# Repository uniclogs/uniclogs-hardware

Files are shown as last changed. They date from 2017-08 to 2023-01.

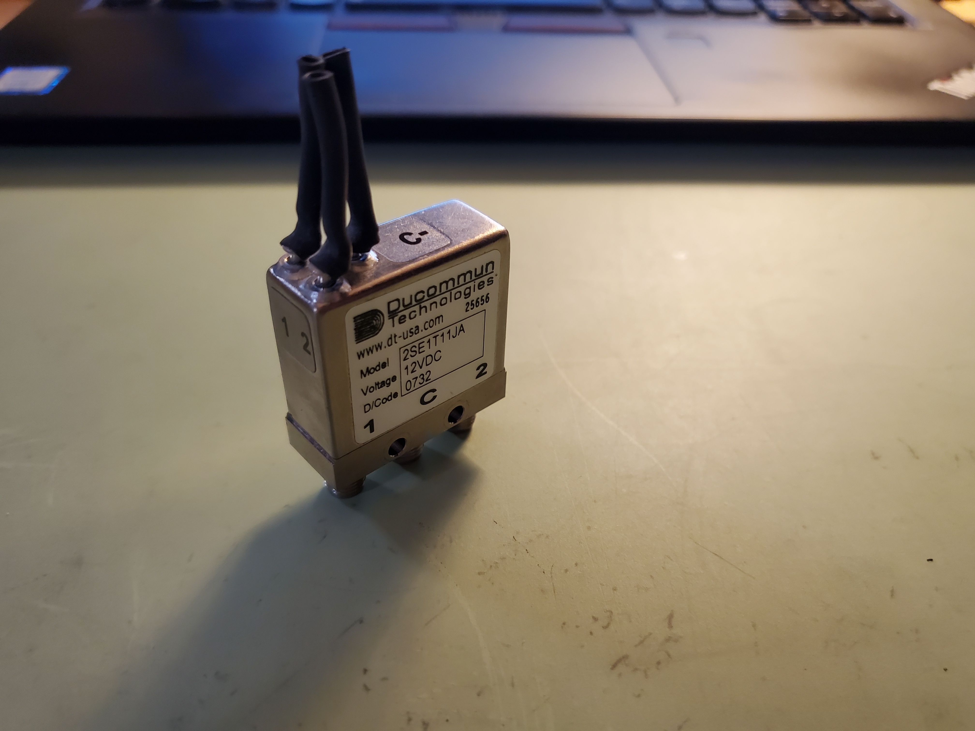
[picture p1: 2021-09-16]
eb-ground-station/rf-systems/components/rf-relay/20210714_223024.jpg

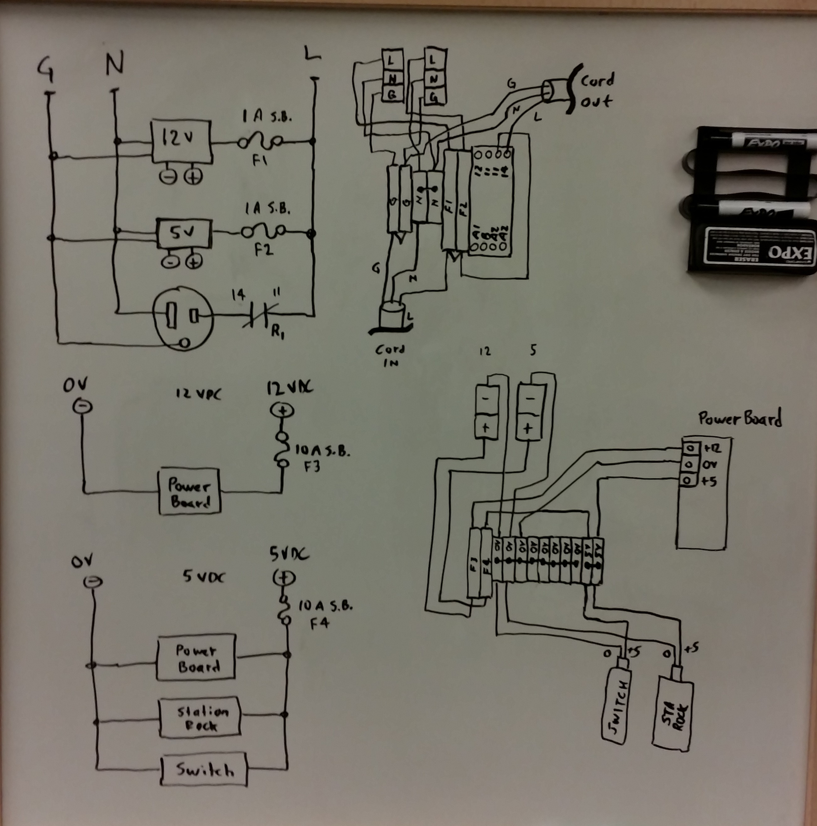
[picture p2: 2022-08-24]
eb-ground-station/power-system/power_wiring_diagram_1a.jpg

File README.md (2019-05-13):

# University Class Open Ground Station
UniClOGS ground station hardware for both RF and antenna positioning

EB Station Block Diagram

EB Station Block Diagram

## OreSat Ground Station Infrastructure

OreSat will utilize two ground stations for this project, a primary station, and a fully-capable secondary station. The primary station is being constructed by the students involved in the project and will be located on the Portland State University Engineering Building. The secondary station is an existing amateur satellite ground station located at a different location for spatial diversity. It can be used to help verify and check out the primary station as construction progresses, and serve as a backup to the primary station. The two stations are identical.

## RF Links

The ground station infrastructure provides two communications functions between the ground and the spacecraft, (1) downlink communications on UHF for the Telemetry Beacons and Command Responses from the spacecraft, (2) uplink communications on L-Band for the Commands to the spacecraft, and (3) downlink communications on S-band for mission payload and camera data.

The UHF component is centered in the 435 to 438 MHz amateur spacecraft service band and utilizes a circular polarized directional Yagi antenna with a RHCP/LHCP polarization sense switch. The L-Band component is centered in the 1260 to 1270 MHz amateur spacecraft service band designated for uplink only, and utilizes a RHCP circular polarized 2x2 helix array. All of this is mounted on an azimuth/elevation antenna positioner. A coax switch connects the UHF antenna to either a Low Noise Amplifier (LNA) for receiving, or a Power Amplifier (PA) for transmitting. The LNA and PA is then connected to a Software Defined Radio (SDR) that provides both UHF RF input and output signals. The L-Band antenna is directly connected to a PA for transmitting only, and then to the same SDR to provide the L Band RF signal.

The S-Band component is centered on 2.4 to 2.43 GHz amateur spacecraft service spectrum. A 0.5 meter parabolic reflector with a RHCP/LHCP feed is mounted on the same antenna positioner as the UHF and L-Band antenna. A coax switch is used to select RHCP or LHCP signal from the feed, is then fed to a bidirectional PA/LNA. The PA/LNA is connected to a ATH9K IEEE 802.11b adapter that provides both the S-Band RF downlink receiver and uplink transmitter signals.

The SDR used for UHF and L-Band is the LimeSDR from LimeMicro, which utilizes GnuRadio for modulation and demodulation. The emission type is GFSK at 50 kb/s, and was chosen for the capability of the Engineering transceiver radio on the spacecraft, an acceptable performance indicated by the link budget, and is somewhat common in the amateur satellite community.

## Antenna positioner

An antenna positioner controller is used to aim the antenna array and is interfaced serially using the EasyComm control protocol accessible through the HamLib control library. The positioner controller is based on the Open Source hardware/software project by K3NG, and provides the ability for tracking control through HamLib _rotctld_ both locally using GPredict, or by the SatNOGS Client software which provides interconnectivity to the SatNOGS system over the Internet.

## GnuRadio 

Data is passed into/out of the ground station radio through GnuRadio ModCod blocks and can provide raw IQ sample files from the payload data. Doppler shift can be compensated for in real time using the tracking software and an XML/RPC server in GnuRadio.

## Data

The Engineering Control/Telemetry subsystem provides telemetry data to the ground in two forms, a GFSK modulated data frame in response to a command request, and a very short Morse code (CW) modulated telemetry sequence and satellite ID if no activity is present for a given period of time. This Morse code ID allows the satellite to be heard by the general amateur radio community and will help with identifying the satellite once on orbit. There are several satellite housekeeping commands that can be sent up from the ground to control power, attitude and payload functions, and most importantly a command to reliably shut off all RF transmissions if required. All commands up to the satellite are authenticated for security.

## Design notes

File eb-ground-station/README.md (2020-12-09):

## EB ground station subsystems

Subsystems pertaining to the Engineering Building "University Class" Open Ground Station (UniClOGS)

Major components

* Structure
* Antennas
* RF systems
* Network
* Power system
* Tracker
* Lightning protection

## BOM for ground station

<!-- [Here is the Bill of Materials so far](https://docs.google.com/spreadsheets/d/1EBKyHZEIYpfHariDGcVJl7H6Yc5BHaDegu6B_IkEdFo/edit#gid=687688620) --->
[Here is the Bill of Materials](https://docs.google.com/spreadsheets/d/1g-H72wh_L9K5FMgDF-K87dqiwulbmqTZjYWP18Jh5gg/edit#gid=1275452567)

The BOM is divided into six sections organizing to some degree what's needed in each phase of the construction.

| Code | Phase of construction |
| --- | --- |
| SDR | Test SDR and GR |
| PANEL | Build station panel |
| POS | Build K3NG positioner controller |
| ANT | Antenna components and feedline |
| ROOF  | Roof structures and appurtenances |
| OPER  | Operations equipment |

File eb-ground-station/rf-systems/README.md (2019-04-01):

## RF Components

* Antennas
* Feedlines
* Low Noise Amplifier
* Power Amplifier
* Software Defined Radio (SDR)

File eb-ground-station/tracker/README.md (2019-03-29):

## Tracker used with UniClOGS

### This is based on the K3NG Rotator Controller

The ground station uses an Arduino and simple interface shield to convert the serial
"Easycom protocol" that _rotctld_ speaks, into the relay output and potentiometer
input expected by the Yaesu G5500 rotator control box.

K3NG has provided an open source solution implementing this Arduino code.

This repo contains some simple instructions on how to get the code, a description of the shield,
and the settings needed by the UniClOGS hardware.

See:  https://github.com/k3ng/k3ng_rotator_controller

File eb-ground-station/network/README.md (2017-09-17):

## Establish OreSat VLAN (aka "Blue Pipe")

- Essentially the "Blue Pipe" is a 1 Gb/s VLAN between the EB Penthouse rack and EB. This is officially called the OreSat VLAN.

- Also related is the edge router and firewall to get us out to the Internet.

### Provide a "what we want" document to Dave Burns to move forward with getting the connection established.

- Dave expects to need a pair of Single Mode SFP's to increase the existing bandwidth over the fiber between the Penthouse switch and the EB switch on LL. He's planning on moving from the MultiMode fiber to SingleMode fiber, since MM over the fiber they have installed won't support Gb over the required distance. They have both MM and SM available at both FTB's. Estimated $250 each.

- Estimate the bandwidth we need given the devices on the roof only push I/Q samples from the SDR to the server in EB-91, and doing all the signal processing on the server. Expected this will go across UDP.

- Describe the protocols and ports we want to move across the VLAN, and what we want to push across the edge router.

   * We expect only ports 22, 123 (NTP) and 443 across the edge router.
   * Essentially answer his question "What are you wanting to put on 'my' network?"
      * Since this is a VLAN, our traffic would never really appear on his network, however what goes out through the firewall and onto the Internet is what he is really asking about.

NB: Dave expressed keen interest in getting NTP from our time server. Maybe also provide PTP?

[Miles started this document](https://docs.google.com/document/d/1XI038USdZ7fAQvtVEo2skS9kDt9Eve8YVRDrkvMqaz0/edit)

### Follow through in getting the LAN physically connected and working.

- There needs to be a 1 Gb/s switch in the rooftop enclosure to provide LAN to both of the GS devices in our enclosure. The weather station will use it's own physical CAT-6 circuit to the Penthouse Cisco switch, so it does not enter onto any of our concerns. 

- There currently is a connection in the EB penthouse using CAT-6 to the rooftop.

- There will need to be a connection in a comm closet adjacent to EB-91 to some structured wiring connection and wall plate on EB-91. It will need to be labeled **_OreSat VLAN_**.

### Establish the OreSat server assets in EB-91

- We should expect to put all of our devices in a small 19 inch rack somewhere in the EB-91 lab

- We will want another 1 Gb/s switch in that rack for all things that need to connect to OreSat VLAN

- There will also need to be a connection back to "Dave's Network" where we connect our edge router between the two. Here another structured wiring jack on EB-91 will be needed, and should be labeled **_Dave's Network_** or something like that.

- I would recommend a Juniper SRX-100 for use as the edge router / firewall for the following reasons.
   * We only need 100 Mb/s out to the Internet.
   * It could setup several security zones
   * Low cost, and highly capable packet filtering

Originally identified this issue on: 20-May-2017

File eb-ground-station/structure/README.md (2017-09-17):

## Requirements for Engineering Building Ground Station Structure
### G.N. LeBrasseur  15-Aug-2017

### Introduction

The Portland State University Aerospace Society and Oregon Small Satellite Project (OreSat) propose
to [augment an existing weather station](weather-station-augmented-design/README.md) on the campus Engineering Building. The weather station is an
existing structure having been in place for several (maybe 4) years, and is in reasonably good physical
condition. It was suggested that this structure could be utilized to provide the physical support for the
proposed satellite ground station antenna on a co-site basis in order to fit within the economic constraints
on the OreSat project.

The design drawing *GS_Structure_1_1* illustrates the existing mast structure, and the proposed changes of
augmenting for the proposed co-site use. Page 3 of 3 of this document indicate the changes in red.

### Expected Loads

The appurtenances or components of the existing weather station have not been described in the drawing, primarily
because it is expected they pose minimal wind or structural load. It is expected that the predominant wind load would be presented
by the ground station antenna array which would be mounted at the top of the augmented structure on page 3 of 3.

The intent of the design is to sustainably survive a continuous wind load of 100 mph or less without damage or failure.

The physical wind load is expected to be within the following:

#### From manufacturer data sheet

 * 70 cm antenna [1] : 2.0 ft^2 at 100 mph
 * 2 meter antenna [2] : 2.5 ft^2 at 100 mph

#### Extended analysis

Upon conversation with the manufacturer it was discovered they did not have a specification of their product for
wind loads with ice. Being in the Pacific Northwest where ice is expected as normal, particularly when wind speeds
might be at their highest, a wind load with ice margin is applied as two (2) times the non-ice wind load value.

So for a wind load with ice safety margin, the following values should be used;

* 70 cm antenna: 2.0 ft^2 at 100 mph * 2 = 4.0 ft^2 at 100 mph
* 2 m antenna:  2.5 ft^2 at 100 mph * 2 = 5.0 ft^2 at 100 mph

**Total wind load: 4.0 + 5.0 = 9.0 ft^2 at 100 mph**

It is thereby anticipated that applying this wind load at the very top hight of the mast as described on page 3 of 3
would describe the extreme structural requirements of this system.

### References

* [70 cm] antenna  
* [2 m] antenna
* 22 foot [cross boom]

[70 cm]: http://www.m2inc.com/amateur/436cp42ug-420-440-mhz/
[2 m]: http://www.m2inc.com/amateur/2mcp22-144-148-mhz/
[cross boom]: http://www.m2inc.com/crossboom-hd-fg-11/

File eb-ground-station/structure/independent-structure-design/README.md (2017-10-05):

# Structural Stuff for the Stand-alone EB Ground Station

As per a conversation between Glenn and Joe on 2017-9-22, we're switching to a slightly smaller set of antennas. 
This lets us drop about 3 ft^2 from the frontal area of each antenna and a few feet of height, while only loosing 3 dB.
There's a [BoM in the tomes of the dark lord Goagh'le.][BoM]

Included are drawings of the roof layout, and the datasheet for the Rohn non-penetrating antenna mount.

[BoM]: https://docs.google.com/spreadsheets/d/1EBKyHZEIYpfHariDGcVJl7H6Yc5BHaDegu6B_IkEdFo/edit#gid=687688620

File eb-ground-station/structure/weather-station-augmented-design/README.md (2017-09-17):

## Utilize existing mast

We want to determine what we need to do to rebuild the station structure in order to co-site both the OreSat ground station, and the weather station maintained by Prof. Elliott Gall.

There is a drawing in this repo that shows both the existing mast structure, and the augmented structure. We should have someone with structural expertise look over this drawing set. The intent is to extend the mast using a 15 foot section of 1-1/4 inch SCH 80 6061 aluminum pipe, and add a set of additional struts. The augmented parts are in red on page 3 of 3 of the set.

## Utilize existing utilities.

* There is a weather rated 120 volt 20 amp duplex GFI receptacle available, and one outlet is used for the weather station. The second outlet could be utilized for our service.

* There are two CAT-6 / RJ-45 receptacles available in a weather rated box, one of which is used by the weather station. The second one could be utilized for our needs. These CAT-6 circuits make their way through structured wiring to the penthouse communications rack, whereby they terminate at a patch panel next to a network switch.

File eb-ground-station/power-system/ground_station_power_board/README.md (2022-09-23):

# Station Power Board

This board controls all of the switching of power to components in the ground station.
It accepts it's commands through an I2C interface on the Stationd computer.

The switching is acomplished through 3 I2C GPIO device setup as 24 output bits. The
bits control mosfet switches provideing both 5VDC and 12VDC circuits.

The board also has an A/D to monitor the RF Power Amplifiers output power detectors. The
characteristics of this power measurement is detailed in the power amplifier testing
spreadsheet unfer RF-systems.

Finally this board provides a temperature measurement of the system enclosures environment.

See further documentation in the docs folder

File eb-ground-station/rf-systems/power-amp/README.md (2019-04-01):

### Linear power amplifier

Power amplifiers using hybrid power amplifier modules from
Mitsubishi or Hitachi are used to drive the antenna.

See:
* 2m:   Hitachi SAV33 MOSFET
* 70cm: Hitachi SAU83L MOSFET
* 23cm: Mitsubishi RA18H1213G
   https://www.mitsubishielectric-mesh.com/products/pdf/ra18h1213g.pdf

Testing data is included in the spreadsheet, including characteristics of the power output monitor voltage.

* 2 meter
   https://www.downeastmicrowave.com/product-p/2m30pack.htm

* 70 cm
   https://www.downeastmicrowave.com/product-p/7025pack.htm

* 23 cm
   https://www.downeastmicrowave.com/product-p/2330pack.htm

Additionally, the output of the LimeSDR is a little too low to fully drive the power amplifires, so inline MMIC
amplifiers are placed in between.

* 2m: MiniCircuits GALI-49 (packed in their development test board TB-409-49+)
   https://www.minicircuits.com/WebStore/dashboard.html?model=GALI-49%2B
   https://www.minicircuits.com/pcb/WTB-409-49+_P02.pdf
    
* 70cm: MiniCircuits GALI-49 (a second one)

* 23cm:  MiniCircuits ZRL-1150LN
   https://www.minicircuits.com/WebStore/dashboard.html?model=ZRL-1150LN%2B

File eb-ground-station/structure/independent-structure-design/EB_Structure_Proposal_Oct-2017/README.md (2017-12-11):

## Proposal for Engineering Building Ground Station
### October 2017

* Narrative of proposal
* General location of site on Engineering Building
* Detailed drawings of site
* Data sheet for non-penetrating mast
* Quote for mast

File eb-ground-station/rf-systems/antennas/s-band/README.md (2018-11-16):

## S Band antenna

* Parabola
* Radome
* 90 degree hybrid
* Testing results

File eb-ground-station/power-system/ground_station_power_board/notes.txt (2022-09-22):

New Design Requirements:
* Use MAX7310ATE 8 bit GPIO expander
* 24 control bits, exact setup TBD
* Switches:
  - Low side
  - High side
  - High side, high current
  - High side, high current, soft start
* Designed in KiCad
* Use the correct I2C RasPi pins
* Connectors; all seperable, push-lock lever or spring type:
  - Power in: 3pos 1row 12AWG
  - GPIO x3 : 8pos 1row 12-26AWG
  - ADC     : 4pos 2row 22AWG
* All 4 UARTs on the pi need to be broken out to their own ports to be passed on to other stuff
* Current ranges should be configurable in hardware after the PCB has been fabbed

Some notes on the new design:
Up to 2 of these boards can be put in paralell simply by connecting the 40pin connectors in paralell and jumping different address jumpers on each board.

Parts: (may be out of date list to what was actually ordered)
+---------------------------------+------------------+-----------------+
| Name                            | MFR              | MPN             |
+---------------------------------+------------------+-----------------+
| 8 pos wire  connector large     | Phoenix Connect  | 1942549         |
| 8 pos wire  connector small     | Phoenix Connect  | 1851290 1966156 |
| 8 pos board connector large     | Phoenix Connect  | 1924143         |
| 8 pos board connector 45° small | Phoenix Connect  | 1827486         |
| 8 pos board connector small     | Phoenix Connect  | 1827923         |
| GPIO expander                   | Maxim Integrated | MAX7310ATE      |
| I2C ADC                         | TI               | ADS1115         |
| I2C temperature sensor          | Microchip        | MCP9808         |
| Dual N-Channel MOSFET           | Diodes Inc       | DMN61D8L-LVT    |
| P-Channel MOSFET                | Vishay Siliconix | SUD50P08-25L-E3 |
| Dual 1.5A MOSFET Driver         | Microchip        | TC427           |
+---------------------------------+------------------+-----------------+

Connectors (Phoenix Connect):
+---------------------------------+---------+------+----+--------+-----+-------------+
| Name                            | Number  | Pins | A  | Pitch  | Ang | Connector   |
+---------------------------------+---------+------+----+--------+-----+-------------+
| 3 pos wire  connector huge      | 1996139 | 3    | 41 | 7.62mm | 0°  | PC 5        |
| 8 pos wire  connector large     | 1942549 | 8    | 16 | 5.08mm | 0°  | MSTB 2,5 HC |
| 8 pos wire  connector small     | 1748419 | 8    | 8  | 3.81mm | 0°  | MC 1,5      |
+---------------------------------+---------+------+----+--------+-----+-------------+
| 3 pos board connector huge      | 1720806 | 3    | 41 | 7.62mm | 0°  | PC 5        |
| 8 pos board connector large     | 1924143 | 8    | 16 | 5.08mm | 0°  | MSTB 2,5 HC |
| 8 pos board connector small     | 1827923 | 8    | 8  | 3.81mm | 0°  | MC 1,5      |
| 8 pos board connector 45° small | 1827486 | 8    | 8  | 3.81mm | 45° | MC 1,5      |
+---------------------------------+---------+------+----+--------+-----+-------------+

Configuration of the Outputs:

Populate and leave some components unpopulated to configure the output current modes.
Only the dual mosfet or the mosfet driver may be populated, never both for the same channel pair
If the dual mosfets are populated, the rest of the circuit may be configred independently for the two channels 
If you populate the dual mosfet, also populate the 1k resistors on its gate.
If you populate the P channel MOSFETs, populate the 10k pullup resistors

Possible current modes: (+ is current out, - is current in)
±1.5A
-500mA
+15A

The channel pair may be configured for EITHER {±1.5A} or {-500mA or +15A}

To configure for:
+---------+-------------+-------------+----------+-------+-----+-------------+
| Mode    | Dual Driver | Dual MOSFET | P MOSFET | Rgate | C   | 2pad jumper |
+---------+-------------+-------------+----------+-------+-----+-------------+
| -500mA  |             | yes         |          |       |     | jumped      |
| +16A    |             | yes         | yes      | 1k    |     | open        |
| 16Asoft |             | yes         | yes      | 680k  | yes | open        |
| ±1.5A   | yes         |             |          |       |     | any         |
+---------+-------------+-------------+----------+-------+-----+-------------+

Use the 3pad jumper to select 5 or 12v for the +15A mode
In soft start mode, adjust Rgate to adjust soft start time

RasPI pins:
  +------------+----+----+------------+
  | 3v3        | 01 | 02 | 5V         |
  | SDA        | 03 | 04 | 5V         |
  | SCL        | 05 | 06 | GND        |
  | TX3        | 07 | 08 | TX0        |
  | GND        | 09 | 10 | RX0        |
  |            | 11 | 12 |            |
  |            | 13 | 14 | GND        |
  |            | 15 | 16 |            |
  | 3v3        | 17 | 18 |            |
  |            | 19 | 20 | GND        |
  | RX4        | 21 | 22 |            |
  |            | 23 | 24 | TX4        |
  | GND        | 25 | 26 |            |
  | TX2        | 27 | 28 | RX2        |
  | RX3        | 29 | 30 | GND        |
  |            | 31 | 32 | TX5        |
  | RX5        | 33 | 34 | GND        |
  |            | 35 | 36 |            |
  |            | 37 | 38 |            |
  | GND        | 39 | 40 |            |
  +------------+----+----+------------+
* UART1 shares pins with UART0

---------------------------------------------------------------------------------------
Deisgn Review Notes:
(probably not me) Part numbers on block diagram on GH readme
(future stuff) clarify where everything (power/data etc) go

X Maybe start with a block diagram where each one goes to the schematic that is that part]
X no 12v top 5v bottom put next to eachother
X 100u on 3.3v out
X change resistors to squiggly ones
X move pullups to where they are used
X add another ferrite bead to 12v input to the 3.3v regulators (may have to be larger)
X To populate: FB1 is bead. FB2 is link. FB3 is link (by 3.3v regulators)
X Seperate dual MOSFETS - QnA and QnB
X Move IO pulldowns to the power page

Design Review Part 2 Notes:
UniClOGS stands for Uiversity Class Open Ground Station
Glen will go in sometime to check the board size
add nuts to render and check clearance, add keepout zone to to holes, remember to include space for nut driver or spacers on the back
add OreSat logo at the very end since it takes a bunch of time to fill
Add 12,5,3.3,gnd .1in header in lower left corner
Assumme we are purcahsing every possible component for the bill of materials
Check connectors for stock
Move vias outside of small passives when possible
Final silkscreen check
Move all siklscreen to match orentation of part
Change all ferrite beads to 0805 size
Ground loop warning note
Change 3.3v to 500mA

ToDo Wed:
Add 12,5,3.3,gnd .1in header in lower left corner
Assumme we are purcahsing every possible component for the bill of materials
Check connectors for stock
Change all ferrite beads to 0805 size

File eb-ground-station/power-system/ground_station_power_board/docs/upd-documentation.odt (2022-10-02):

UniClOGS Power Delivery Board

Description and Configuration Details - Board rev 2

Benjamin Crall Sep-2022 Doc Rev. 2.0

# Power Outputs:

Output channels can be configured for one of several modes. Output configuration is done by populating or leaving some other components unpopulated. A + denotes a current leaving the board, and a - denotes a current entering the board. Note that all banks do not support all current modes. Do not populate components that are not specified. Ensure that the output current from all outputs on each power input does not exceed the maximum input current.

## Bank A:

### Available modes:

- -500mA
- +16A
- +16A with soft start

### Configuration Instructions:

The channel supports 12-24AWG wire

Each channel may be configured independently

If you populate the P channel MOSFETs, populate the 10k pullup resistors

Use the 3pad jumper to select 5 or 12v for the +16A mode

In soft start mode, adjust Rgate to adjust soft start time

Mode | Dual MOSFET | P MOSFET | Rgate | C | 2pad Jumper
-500mA | Yes | | | | Jumped
+16A | Yes | Yes | 1k | | Open
+16A soft-start | Yes | Yes | 680k | Yes | Open

## Bank B and C:

### Available Modes:

- ±1.5A
- -500mA

### Configuration Instructions:

These channels support 16-26AWG wire

A channel pair is an even channel and the next odd channel (e.g. 0 and 1)

Each channel pair must be configured for the same mode.

Mode | Dual Driver | Dual MOSFET
-500mA | | Yes
±1.5A | Yes

# Power Inputs

## Input:

Power is supplied to the 3 position connector on the left edge of the board. The pinout is

+12V 25A

GND 16A

+5V 16A

The board does not draw or provide any power to the raspberry pi

Each input supports 8-24AWG wire.

## Protection:

Each power input has reverse polarity protection.

There is no overcurrent protection. Be sure to not to draw too much current from single or combination of outputs. See the channel documentation above to see the individual channel output currents.

- Channel A supports up to 18A of total output current on 5V
- Channel A and B share 18A of total output current on 12V
- Channel C has 7A of total output current at 12V independent of channels A and B

## Outputs:

Power indicator LEDs are in the lower left corner of the board. Next to them are power output pins. These pins are capable of 1A each, except for 3.3V which is capable of 250mA

# Analog Inputs

## Main Inputs

Each board has 4 analog inputs available on the top left 8 pin connector. The pinout is

ADC0 | Agnd | ADC1 | Agnd | ADC2 | Agnd | ADC3 | Agnd

Agnd is connected to general ground by the left link at the top of the Analog In section. This link can be replaced by a 0805 ferrite bead if desired.

Be careful to avoid ground loops when connecting to the Agnd pins

## .1” Inputs

The analog inputs are also available on the .1” header above the main connector. The pinout of this connector is

ADC0 | ADC1 | ADC2 | ADC3 | Agnd

# Data Connectors

## 1x IDC 40 pin connector for the Raspberry pi

| 01 | 02
SDA1 | 03 | 04
SCL1 | 05 | 06 | GND
TX3 | 07 | 08 | TX0
GND | 09 | 10 | TX0
TMP_ALERT (GPIO17) | 11 | 12
ADC_RDY (GPIO27) | 13 | 14 | GND
| 15 | 16
| 17 | 18
| 19 | 20 | GND
RX4 | 21 | 22
| 23 | 24 | TX2
GND | 25 | 26
TX2 | 27 | 28 | RX2
RX3 | 29 | 30 | GND
IO_RESET (GPIO6) | 31 | 32 | TX5
RX5 | 33 | 34 | GND
| 35 | 36
| 37 | 38
GND | 39 | 40

The 3.3V and 5V pins on the Raspberry Pi are not connected

## 4 pin I²C1

GND | 3.3V | SCL1 | SDA1

This is the internal I²C bus used to communicate with the card

## 4 pin (2x2) Signals

ADC_RDY | TMP_ALERT
IO_RESET | gnd

## 3 pin Serial

gnd | RX (in) | TX (out)

These headers connect to (from top to bottom) UART0, UART2, UART3, UART4, UART5

UART2 can also double as I²C0. To use this as I²C0, populate R4 and R5, otherwise leave them empty

gnd | SCL0 | SDA0

# Signal Configuration

All I²C devices on the board are connected to I²C1 on the Raspberry Pi.

## Power Output Banks

The power output banks are controlled by MAX7310 I²C expanders. Each power output bank can be configured to 1 of 8 I²C addresses. The I²C address for each bank is between 0x20 and 0x27. The 3 jumpers configure the 3 lower bits of the address, and the binary address is 0100{AD2}{AD1}{AD0}. The default jumpers connect the address pins to SCL (0) and SDA (1). See the datasheet if more addresses are required. Banks A,B and C have the default addresses of 0x20, 0x21, and 0x22. The active low IO_RESET signal is connected to the Raspberry Pi. Ensure that this signal is held high through boot to not reset the expanders. IO_RESET is pulled high by a 4.7k resistor. See the datasheet for device usage.

## ADC

The ADC is an ADS1115IDGS I²C ADC with a default address of 0x48. Use the jumper to select the alternate address of 0x49 if required. The active low ADC_RDY signal is connected to the Raspberry Pi connector. ADC_RDY is pulled high by a 4.7k resistor. See the datasheet for device usage.

## Temperature Sensor

The temperature sensor is an ADT7410TRZ I²C Temperature Sensor. The default address is 0x4A. Use the left jumper to select the alternate address of 0x4B if required. Note that only the A0 pin is used and the A1 pin is tied to 3.3V to avoid address conflicts with the ADC. Additionally, the sensor can also create two alert or alarm signals which are active low and connected to TMP_ALERT. Use the right jumper to select between the “Critical Overtemperature” (CT) and “Overtemperature and Undertemperature” (INT) signals. TMP_ALERT is pulled high by a 4.7k resistor. See the datasheet for device usage.

# Using Multiple Boards

Two of these boards may be used in together to provide additional output channels. To do this, the first board should be configured in the default configuration. On the second board:

- Change the AD2 jumper on each bank from 0 to 1. Banks A, B, and C will now be on I²C addresses 0x24, 0x25, and 0x26
- Change the address jumper on the ADC to 0x49
- Change the address jumpers on the temperature sensor to 0x4B
- Connect the 40 pin IDC connector to both boards in parallel
  - Alternately, connect the 4 pin (2x2) Signals connector and the 4 pin (1x4) I²C1 connector except for the 3.3V pin directly between the two boards

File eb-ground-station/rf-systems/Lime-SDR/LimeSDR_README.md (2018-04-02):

# LimeSDR Setup

To get a LimeSDR working on a linux-based system, there are several different components that need to be installed depending on what functionality is wanted.

This document focuses on getting LimeSDR working with gnuradio based setups.

## The Components
### LimeSuite
The first component needed for interfacing with a LimeSDR is LimeSuite, provided by MyriadRF. This component includes all drivers needed to interface with the board, and provides the `LimeUtil` and `LimeSuiteGUI` tools. `LimeUtil` allows command line programming and updating of the LimeSDR, while `LimeSuiteGUI` is a simple to use frontend for manually manipulating the various registers and parameters of the board. However, `LimeSuiteGUI` is not required for the other components to work with it. It's just a graphical frontend to manually manipulate parameters for testing.

In addition to the tools provided, LimeSuite provides a plugin for the next component, SoapySDR, which allows it to interface with the LimeSDR through the drivers.

### SoapySDR
This component is a generalized SDR interface library, usable with many different SDRs. Interfaces are provided to the various SDRs through plugins for SoapySDR. LimeSuite provides the plugin for LimeSDR, allowing SoapySDR compatible things to interface with the LimeSDR.

### GrOsmoSDR
gnuradio and PothosSDR use osmocom's source and sink blocks. GrOsmoSDR provides gnuradio with the interface to SoapySDR.

## Putting it together
### Arch Linux
On Arch Linux, I had to install `soapysdr-git` `limesuite-git` and `gr-osmosdr-git` in order to get the full data path working. I also installed `gqrx-git` in order to test the LimeSDR with GQRX.

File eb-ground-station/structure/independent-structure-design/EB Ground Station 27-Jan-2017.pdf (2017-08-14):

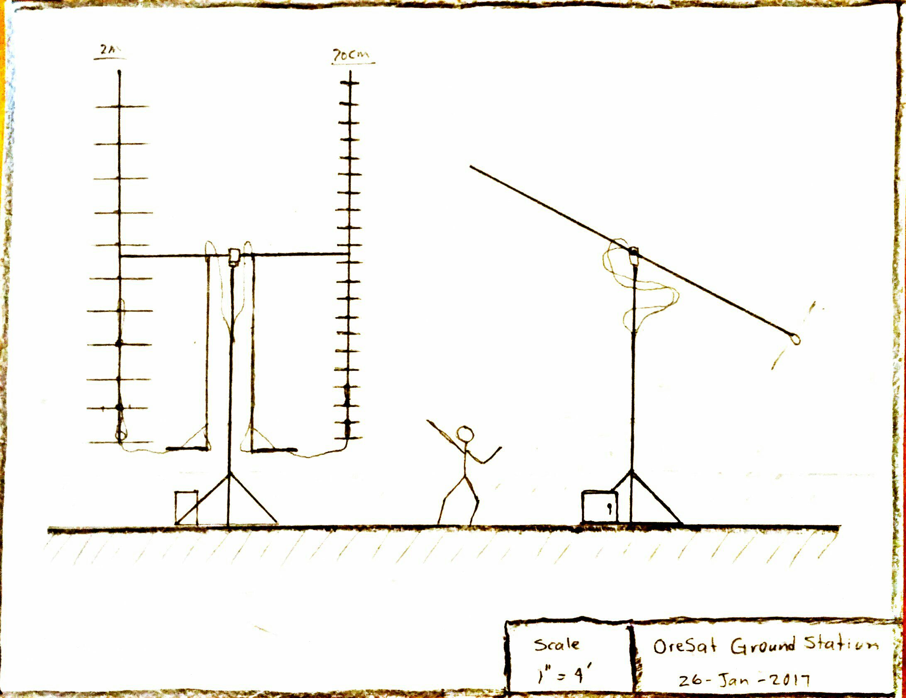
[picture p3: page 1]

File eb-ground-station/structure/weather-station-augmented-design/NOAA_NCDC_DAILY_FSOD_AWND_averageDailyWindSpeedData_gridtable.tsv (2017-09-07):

T | NOAA NCDC DAILY FSOD AWND
julian_day | mph
5.8857338E-41 | 8.100000
5.8858739E-41 | 8.600000
5.8860141E-41 | 8.400001
5.8861542E-41 | 5.800000
5.8862943E-41 | 5.300000
5.8864345E-41 | 4.700000
5.8865746E-41 | 5.800000
5.8867147E-41 | 3.600000
5.8868548E-41 | 9.900001
5.8869950E-41 | 9.400001
5.8871351E-41 | 2.700000
5.8872752E-41 | 4.300000
5.8874154E-41 | 8.000000
5.8875555E-41 | 17.70000
5.8876956E-41 | 13.80000
5.8878358E-41 | 3.500000
5.8879759E-41 | 12.80000
5.8881160E-41 | 9.200000
5.8882561E-41 | 7.800000
5.8883963E-41 | 9.900001
5.8885364E-41 | 8.400001
5.8886765E-41 | 9.400001
5.8888167E-41 | 15.00000
5.8889568E-41 | 13.70000
5.8890969E-41 | 8.600000
5.8892371E-41 | 5.400000
5.8893772E-41 | 4.600000
5.8895173E-41 | 2.700000
5.8896574E-41 | 5.800000
5.8897976E-41 | 7.200000
5.8899377E-41 | 5.200000
5.8900778E-41 | 5.000000
5.8902180E-41 | 3.100000
5.8903581E-41 | 3.500000
5.8904982E-41 | 10.40000
5.8906384E-41 | 12.40000
5.8907785E-41 | 6.400000
5.8909186E-41 | 11.90000
5.8910587E-41 | 10.80000
5.8911989E-41 | 17.30000
5.8913390E-41 | 13.80000
5.8914791E-41 | 10.40000
5.8916193E-41 | 10.70000
5.8917594E-41 | 8.600000
5.8918995E-41 | 8.800000
5.8920397E-41 | 8.500000
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

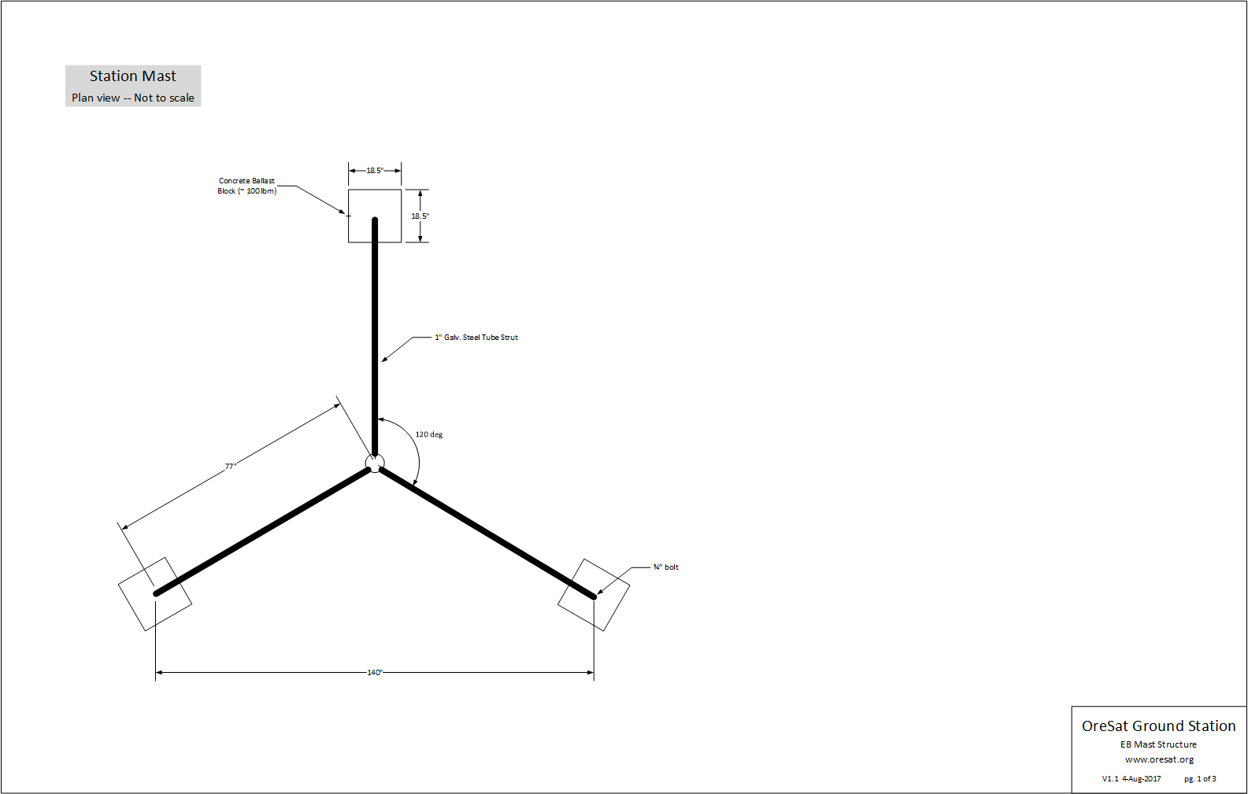
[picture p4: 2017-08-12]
eb-ground-station/structure/weather-station-augmented-design/GS_Structure_1_1.png

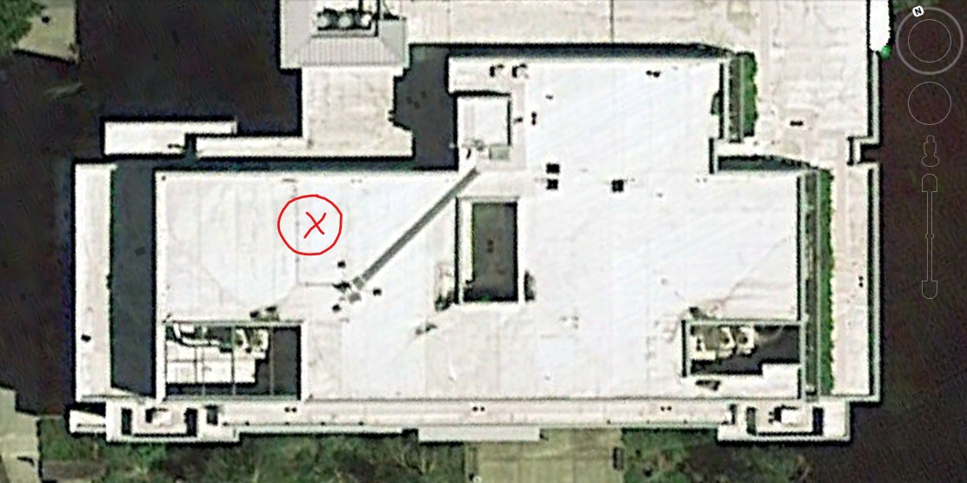
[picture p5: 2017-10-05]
eb-ground-station/structure/independent-structure-design/EB_Structure_Proposal_Dec-2017/EB_Station_annotated.jpg

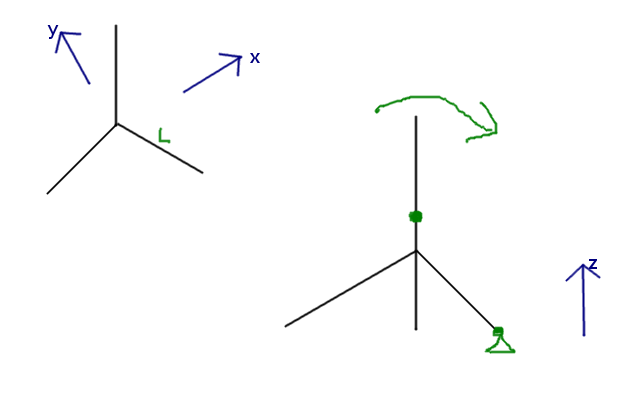
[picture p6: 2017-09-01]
eb-ground-station/structure/weather-station-augmented-design/loadingDiagram.png

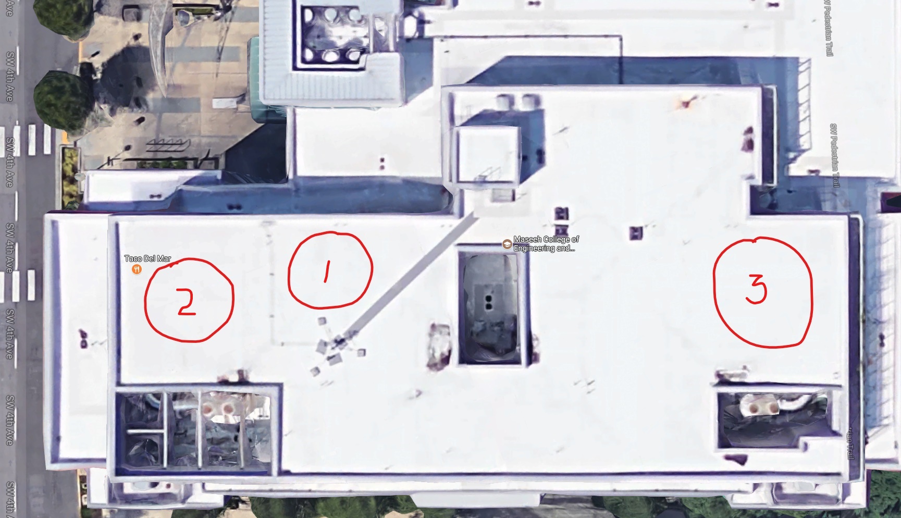
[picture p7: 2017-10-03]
eb-ground-station/structure/independent-structure-design/EB_Roof_2017-09-13_annotate.jpg

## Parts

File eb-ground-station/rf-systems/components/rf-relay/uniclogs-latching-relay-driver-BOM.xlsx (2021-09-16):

UniClOGS Latching Relay Driver Board v1.0 BOM revision ~~ 0 ~~ 1
Qty | Parts | MFR | MPN | Description | DIST | DPN | P/NP | Notes
1 | C1 | Panasonic | EEV-FK1H471M | CAP ALUM 470UF 20% 50V SMD | Digi-Key | P19506CT-ND | P | Rev 0
1 | RV1 | TDK Electronics | B72540V1140S262 | VARISTOR 22V 1.2KA 2220 | Digi-Key | 495-1461-1-ND | P | Rev 0
2 | D1, D2 | Diodes Incorporated | S1G-13-F | DIODE GEN PURP 400V 1A SMA | Digi-Key | S1G-FDICT-ND | P | Rev 0
1 | C1 | Rubycon | 50TRV470M16X16.5 | CAP ALUM 470UF 20% 50V SMD | Digi-Key | 1189-3572-1-ND | P | Updated 15-Sep-2021 – Rev 1
1 | RV1 | AVX Corporation | VJ15PA0160KBA | VARISTOR 2220 24.5 V 1.5 kA | Digi-Key | 478-13175-1-ND | P | Updated 15-Sep-2021 – Rev 1
2 | D1, D2 | Diodes Incorporated | S1G-13-F | DIODE GEN PURP 400V 1A SMA | Digi-Key | S1G-FDICT-ND | P | Updated 15-Sep-2021 – Rev 1

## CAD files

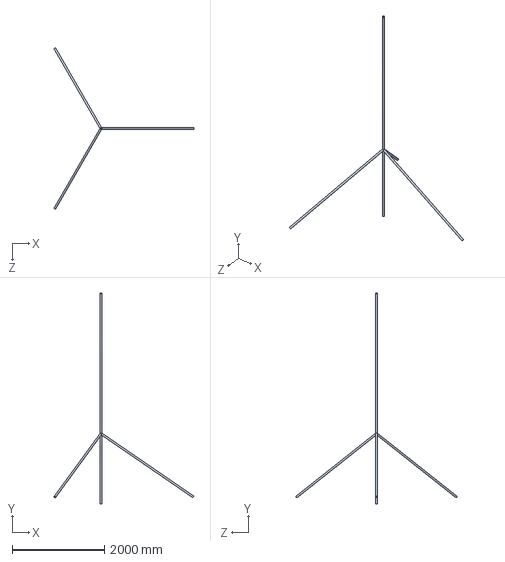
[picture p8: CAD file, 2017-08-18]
eb-ground-station/structure/weather-station-augmented-design/SW-CAD/First_order_Approximate_mast_loading.SLDPRT
3032.8 x 4572.0 x 3495.5 mm

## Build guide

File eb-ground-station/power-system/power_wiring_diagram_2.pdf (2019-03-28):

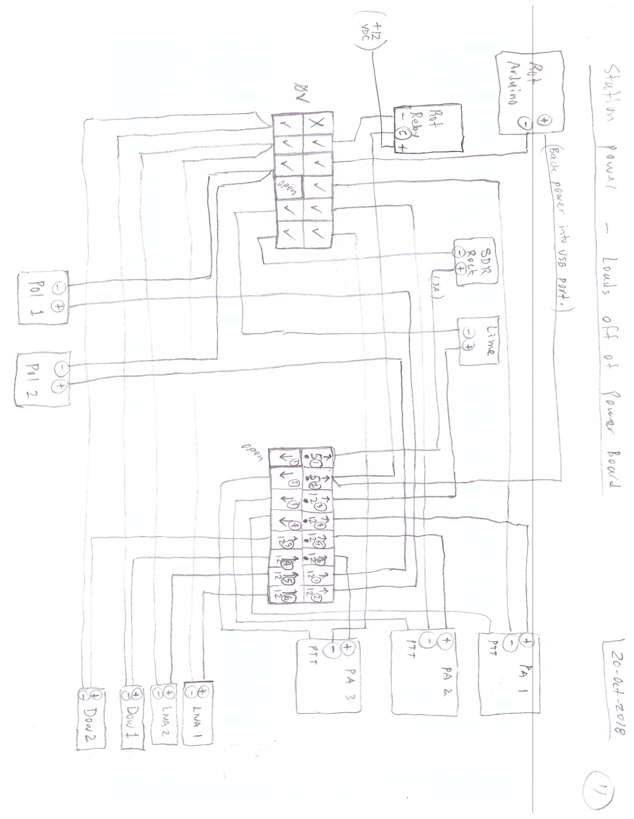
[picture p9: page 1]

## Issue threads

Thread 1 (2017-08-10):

Evaluate EB weather station for OreSat ground station use

glennl, 2017-08-10:
## Utilize existing mast

We want to determine what we need to do to rebuild the station structure in order to co-site both the OreSat ground station, and the weather station maintained by Prof. Elliott Gall.

There is a drawing in this repo that shows both the existing mast structure, and the augmented structure. We should have someone with structural expertise look over this drawing set. The intent is to extend the mast using a 15 foot section of 1-1/4 inch SCH 80 6061 aluminum pipe, and add a set of additional struts. The augmented parts are in red on page 3 of 3 of the set.

## Utilize existing utilities.

* There is a weather rated 120 volt 20 amp duplex GFI receptacle available, and one outlet is used for the weather station. The second outlet could be utilized for our service.

* There are two CAT-6 / RJ-45 receptacles available in a weather rated box, one of which is used by the weather station. The second one could be utilized for our needs. These CAT-6 circuits make their way through structured wiring to the penthouse communications rack, whereby they terminate at a patch panel next to a network switch.

glennl, 2018-08-07:
We went the route of building our own mast, non-penetrating base rack, and enclosure. The weather station would have been really difficult to convert given our wind loads, not to mention difficult to co-exist with very dissimilar equipment.

Closed 2018-08-07.

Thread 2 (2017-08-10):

Establish OreSat VLAN (aka "Blue Pipe")

glennl, 2017-08-10:
## Establish OreSat VLAN (aka "Blue Pipe")

- Essentially the "Blue Pipe" is a 1 Gb/s VLAN between the EB Penthouse rack and EB. This is officially called the OreSat VLAN.

- Also related is the edge router and firewall to get us out to the Internet.

### Provide a "what we want" document to Dave Burns to move forward with getting the connection established.

- Dave expects to need a pair of Single Mode SFP's to increase the existing bandwidth over the fiber between the Penthouse switch and the EB switch on LL. He's planning on moving from the MultiMode fiber to SingleMode fiber, since MM over the fiber they have installed won't support Gb over the required distance. They have both MM and SM available at both FTB's. Estimated $250 each.

- Estimate the bandwidth we need given the devices on the roof only push I/Q samples from the SDR to the server in EB-91, and doing all the signal processing on the server. Expected this will go across UDP.

- Describe the protocols and ports we want to move across the VLAN, and what we want to push across the edge router.

   * We expect only ports 22, 123 (NTP) and 443 across the edge router.
   * Essentially answer his question "What are you wanting to put on 'my' network?"
      * Since this is a VLAN, our traffic would never really appear on his network, however what goes out through the firewall and onto the Internet is what he is really asking about.

NB: Dave expressed keen interest in getting NTP from our time server. Maybe also provide PTP?

[Miles started this document](https://docs.google.com/document/d/1XI038USdZ7fAQvtVEo2skS9kDt9Eve8YVRDrkvMqaz0/edit)

### Follow through in getting the LAN physically connected and working.

- There needs to be a 1 Gb/s switch in the rooftop enclosure to provide LAN to both of the GS devices in our enclosure. The weather station will use it's own physical CAT-6 circuit to the Penthouse Cisco switch, so it does not enter onto any of our concerns.

- There currently is a connection in the EB penthouse using CAT-6 to the rooftop.

- There will need to be a connection in a comm closet adjacent to EB-91 to some structured wiring connection and wall plate on EB-91. It will need to be labeled **_OreSat VLAN_**.

### Establish the OreSat server assets in EB-91

- We should expect to put all of our devices in a small 19 inch rack somewhere in the EB-91 lab

- We will want another 1 Gb/s switch in that rack for all things that need to connect to OreSat VLAN

- There will also need to be a connection back to "Dave's Network" where we connect our edge router between the two. Here another structured wiring jack on EB-91 will be needed, and should be labeled **_Dave's Network_** or something like that.

- I would recommend a Juniper SRX-100 for use as the edge router / firewall for the following reasons.
   * We only need 100 Mb/s out to the Internet.
   * It could setup several security zones
   * Low cost, and highly capable packet filtering

Originally identified this issue on: 20-May-2017

jameysharp, 2017-08-11:
I assume @heliochronix should be tagged on this issue too, then.

You can't really estimate SDR bandwidth unless you've either already selected radio hardware (in which case you can use its interface speed as an upper bound, like USB2's 480Mbps) or you know what radio bandwidth you want to capture (so you can multiply that by 2 for Nyquist and times, say, 16 bits per sample). Do we have either of those?

I've made some edits to Miles' document, and I'd like to review it again before it's submitted, so please ping me when you're ready?

jameysharp, 2017-08-11:
We should put some thought into how to distribute data between ground stations, since our choice of network protocol there may be of interest to network admins. I guess the draft currently suggests just using HTTP(S).

I'm tempted to suggest peer-to-peer approaches like BitTorrent or the [Inter-Planetary File System](https://ipfs.io/); the latter is a clear winner based solely on its name, obviously. 😉 In both cases, the CAT might see us exchanging some amount of [µTP](https://en.wikipedia.org/wiki/Micro_Transport_Protocol) traffic over UDP, possibly on random ports. For IPFS they might instead see TCP port 4001.

More generally, we need to discuss what our requirements are for telemetry, including threat model (e.g. does any of it need to be secret?). And aren't we also supposed to capture telemetry for other groups in return?

jameysharp, 2017-08-11:
Why do we need a $350 router instead of just using a server with two Ethernet ports and configuring firewall and routing in Linux?

What equipment do you expect to have in the rack downstairs that we'd need a switch for?

glennl, 2017-08-11:
Yes, actually that would be fine. I just threw an SRX100 in there so the firewall / router could be managed completely independently from whatever we put on our LAN. I have been finding used H2 models on eBay for around $100 +/-.

The Linux box is a great solution too, and could also run an IDS like snort. I think we should choose whatever works best for the group supporting our network security.

Regarding the switch: I expect one (1 Gb/s) VLAN to come into our lab space through structured wiring (jack on the wall). On that VLAN we need our server (at 1Gb/s), and the firewall that goes to Dave's LAN, so that adds up to 3 ports, at least two of which are 1 Gb/s. I would also expect there may be other desires over time to put things (like a laptop or two) on our VLAN as well, so I simply would specify an 8 port Gb switch. Those are easily available for $25 on Amazon.

I will post the "Blue Pipe" drawing here in a minute.

glennl, 2018-08-07:
The OreSat VLAN is up and running. On 4-Jul-2018 Miles ran _iperf_ to confirm the connection.
Server to Roof-Rock64: **940 Mb/s**
Roof-Rock64 to Server: **799 Mb/s**
The connection was made using the existing MultiMode fiber connection and SFP's even though Dave mentioned he would change out the connection to Single Mode. I expect we are okay with the bitrate we have, and can just leave it as is.

Closed 2018-08-07.

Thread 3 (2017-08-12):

Order parts needed for the EB ground station

glennl, 2017-08-12:
## BOM for ground station

[Here is the Bill of Materials so far](https://docs.google.com/spreadsheets/d/1EBKyHZEIYpfHariDGcVJl7H6Yc5BHaDegu6B_IkEdFo/edit#gid=0)

The BOM is divided into six sections organizing to some degree what's needed in each phase of the construction.

| Code    | Phase of construction                       |
| ---------- | ----------------------------------------------- |
| SDR     | Test SDR and GR                             |
| PANEL | Build station panel                            |
| POS     | Build K3NG positioner controller      |
| ANT     | Antenna components and feedline   |
| ROOF  | Roof structures and appurtenances |
| OPER  | Operations equipment                      |

glennl, 2018-08-07:
Parts have been ordered and almost everything has been received for the primary station functionality. There are additional tabs on the spreadsheet for orders placed after the original. Glenn needs to put together a new _Master BOM_ that reflects all items purchased that are not included on these BOM sheets.

Closed 2019-03-19.

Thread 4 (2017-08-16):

SatNOGS: Punch holes into positioner enclosure

glennl, 2017-08-16:
### Punch holes into the enclosure for AZ and EL axis booms.
 * Glenn has a chassis punch tool if needed

glennl, 2018-08-07:
Chuck has taken on this part of the project, and it has been completed.

Closed 2018-08-07.

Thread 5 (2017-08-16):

SatNOGS:  Free up AZ and EL gear mechanism

glennl, 2017-08-16:
It has been discovered that the AZ and EL gear mechanisms that were 3D printed seem to bind so much that the stepper motors cannot move the assembly.

glennl, 2018-08-07:
Chuck and Oliver worked on this and resolved the problem. New gears were printed.

Closed 2018-08-07.

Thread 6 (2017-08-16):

SatNOGS: Replace N connector on helix antenna

glennl, 2017-08-16:
### Final work needed on the helix antenna
* Replace N connector
* Paint portions of it black

glennl, 2017-09-04:
N connector has been replaced.

glennl, 2018-08-07:
* Mark replaced the N connector and it is acceptable. The connector type purchased was very susceptible to being over heated and melting.
* Chuck completed the painting work.
* Nathalie confirmed the antenna is working acceptably.

Closed 2018-08-07.

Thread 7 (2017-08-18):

Stress analysis of EB-ground-station needs to be performed

jalouke, 2017-08-18:
@Joedang you should pick up where I left off. I found out that the wind load of the antenna with ice is 460 lbf. I started a file for a nice approximation and did a static loading of it using the above load. The fixtures at the base may not be entirely accurate (the center post is not fixed or pinned in any way). Please get with @glennl and discuss what needs to be done to get this more accurate.

glennl, 2017-08-19:
### Look at the following options
* Increased pipe diameter of 6061 Al
* Different material other than 6061-T6 Aluminium, such as chromoly [1] steel. It is understood there are consequences for this material
  * Insane cost
  * Tubing dimensions, not pipe
  * Availability lead time (if even possible) in the needed diameter
[1] https://en.wikipedia.org/wiki/41xx_steel

glennl, 2017-08-25:
I have placed photos of the EB weather station taken on 2-Jun-2017 into our OreSat Google Drive under **OreSat EB Ground Station > Weather Station Photos**. These should be useful to understand what is presently on the site.

Joedang, 2017-09-01:
@jalouke were you using the simulation add-in for SW?

jalouke, 2017-09-01:
yup, if you open the part in solidworks 2016 there will be a static tab at the bottom with the analysis that I did.

jalouke, 2017-09-01:
oops, pushed the wrong button

Joedang, 2017-09-07:
I have some questions about the wind loading. @jalouke, did you put the calculations for that 460 lbf figure somewhere? (I'm assuming you found a reasonable source for the drag coefficient for antennas and used the frontal area quoted by the manufacturer.)

@glennl, I know you showed/told me the manufacturer's quote for the frontal area with ice, but I don't remember where to find that or if I wrote it down at all. Do you have that? Also, do you know the manufacturer/model of the antenna and/or do you have a data sheet for it?

glennl, 2017-09-07:
@Joedang, I burried down here...
https://github.com/oresat/oresat-ground-station/blob/master/eb-ground-station/GS_Structure_Requirements_1_1.md

glennl, 2017-09-09:
@Joedang
Here are some links I came across pertaining to wind and ice loads:

* [Where we can buy the TIA-222-G standard for big $$$](http://www.tiaonline.org/all-standards/committees/tr-14)
* [An online document describing some stuff in TIA-222-G](http://www.towernx.com/downloads/TIA-222-G_Explained.pdf)
* [City of Portland page on tower structures](https://www.portlandoregon.gov/bds/article/505592)
* [Design or structural evaluation of supports for highway signs, luminaires, and traffic signals](http://highways.transportation.org/documents/sec03-lts-5trev.pdf)
* [Calculating wind load](http://sciencing.com/calculate-wind-loads-wind-speeds-6104140.html)
* [A Comparison of Wind and Ice Loads for the Design of Transmission Lines](http://iwais.compusult.net/html/IWAIS_Proceedings/IWAIS_2011/Papers/P1_34_227.pdf)
* [Ice loads](http://www.ce-ref.com/Load/ICE/ASCE%207_05_ice/ASCE_7_05_ice.html)

glennl, 2018-08-07:
The decision was made to go with a Rohn JRM27510 and loading it with 950 lbm of ballast. This provides Vmax of 97 mph.

Closed 2018-08-07.

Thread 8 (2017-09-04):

SatNOGS: Build and test controller board

glennl, 2017-09-04:
### Notes

#### Osh Stencils for solder stencil
https://www.oshstencils.com/

#### SatNOGS controller link:
The main schematic is satnogs_controller.sch and is in the following link.
https://github.com/satnogs/satnogs-rotator-controller/tree/master/PCB/satnogs_controller

21-Jul-2017  Mark M.
The encoder schematic (the purpose of which I do not understand. Which part of the block diagram you made was that?) is in the following link with file name encoder_as5040.sch

https://github.com/satnogs/satnogs-rotator-controller/tree/ master/PCB/SatNOGS_Encoder/encoder_as5040

20-Jun-2017  Glenn L.
Andrew has ordered them.
I am having a hard time wrapping my arms around this controller.
Probably because I am not using KiCad?

20-Jun-2017  Glenn L.
Katia has parts?
No she does not, they still need to be ordered...

glennl, 2017-09-04:
At this point we have remaining "issues"

* Program Arduino Pro Mini
* Communication between Arduino and Ras Pi

glennl, 2018-01-09:
From Zulip covering this particular single issue:
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

Closed 2019-03-19.

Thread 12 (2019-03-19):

Power Board - E1/E2 'NAME' reversed

glennl, 2019-03-19:
E1/E2 'NAME' reversed on power board [Oliver]

Closed 2023-01-15.

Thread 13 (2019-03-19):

Power Board - I2c error

glennl, 2019-03-19:
When switching power to the Lime SDR, there is a huge disturbance on the I2C bus. This was noticed when command responses were being acted upon. It appears to only be significant when the LimeSDR power is switched.

The disturbance is a -2V and +3V disturbance at about 4 uS. Then there is ringing at about 500 kHz following that.

Photos on Slack...

glennl, 2019-03-19:
Figure out power board issues
* Power bump
   * Filter; ___No, worsens problem with back-emf___
   * Slow-start; ___Worked quite well, and we think it fixed the problem___
* i2c issue

oliver-rew, 2019-04-19:
Can we completely isolate the rock64 and maybe even the GPIO expander, from the rest of the board?

oliver-rew, 2019-04-19:
For powering the GPIO expander, we could either pull power from the rock64, or put an isolated power supply on the board?

Closed 2023-01-15.

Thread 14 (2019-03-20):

Power Board - Create BOM

glennl, 2019-03-20:
The BOM for this board currently consists of several DigiKey carts posted by Oliver in Zulip. This needs to be put into the "PSAS BOM Format" and placed here.

Closed 2023-01-15.

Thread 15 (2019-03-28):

Power Board - Rev. 2 wish list

glennl, 2019-03-28:
This is a list of things to be included in revision 2 of the power board.

**_We are declaring that the power board must be moved to Rev. 2 before our satellite is manifested._**

* Soft starts circuits on all P-Channel outputs.
* Move the Station Rock-64 UART that communicated with the Tracker Arduino to UART #1. This is done on the 40 pin connector. Also be sure to not include any other Rock-64 pins in the connector to reduce interference.
* Bring UART #2 out on pins for use as a Rock-64 console. (Connect this to an independent serial device server?)
* A watchdog of some form to manage the GPIO controller?
* Anything else?

oliver-rew, 2019-04-19:
We discussed this, but when we first built the board we noticed there was miscommunication between us. You though we were putting in a UART terminal block and I thought you wanted just pin headers. If you want terminal blocks, we should add them.

oliver-rew, 2019-04-22:
We should opto-isolate the GPIO expander from all the power circuits. We could remove the power regulator and pull power and ground from the Rock64, then we can isolate the entire I2C bus and GPIO expander from everything else. The one weird thing could be the ADC, which is on the I2C bus but whose ground it referenced to the power side. Maybe use a i2c isolator?

glennl, 2019-04-24:
> We discussed this, but when we first built the board we noticed there was miscommunication between us. You though we were putting in a UART terminal block and I thought you wanted just pin headers. If you want terminal blocks, we should add them.

The pin header is just fine. Actually I like how you made it fit a common FTDI header, so I would actually now choose this over my original idea. Let's keep it as it is.

Closed 2023-01-15.

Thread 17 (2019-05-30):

Enclosure - Replace with larger SS type

glennl, 2019-05-30:
#### The EB Groundstation Enclosure has been determined to be too small for the equipment housed in it causing a maintenance struggle, and of a material not conducive to being exposed to high levels of sunlight causing considerable increased internal temperature during sunny days.

We have a potential solution for the enclosure thermal issue, and a test to confirm this that is ready to go up onto the roof.

Some background discussion;
• The amount of equipment in this enclosure is a considerable up-scope from the initial design. This demonstrates the notion that one should never choose an enclosure until all design work is complete, and then future room to expand-into should be considered. We were even adding things as late as last week, and Miles and I have plans to add "just one last thing!" This enclosure may have been chosen too early in haste and I am fully responsible for that, but it had to be done at that early time.
• Other than possibly helping to reduce thermal extremes, a larger enclosure would allow easier access to components for maintenance, and provide a neater more professional appearance. Being as full as our enclosure is, you can't really see how neat things really are down under all the layers. :upside_down_face:
• From my (_bragging => significant experience_) with enclosures outdoors, the best way to learn how dirty Portland air is would be to put a thermostatically controlled fan pulling external air through a filter onto an enclosure. Even up on a roof, the dirt ingested is significant. Fans pulling external air are totally acceptable for indoor (server, telecom, equipment) rooms, but when outdoors other solutions are needed.
• My experience shows enclosures made out of stainless steel do a lot better when exposed to direct sunlight. SS is quite reflective, and also a somewhat poor thermal conductor. Whereas I have seen many enclosures get up to 50 deg C (like ours does now) year after year, and the equipment continues to work reliably (even radio equipment) the SS enclosures often peak out at around 10 to 15 degrees cooler. (That is hint #1)
• Temperatures getting up to what we are seeing is unacceptable when there are batteries (especially large storage batteries) or things that are particularly susceptible to drift over temperature such as analog or frequency processing. Yes, Miles and I are also thinking about adding a GPS disciplined local oscillator, but we are not seeing frequency drift at this time.
• So it is said, "_any good idea without supporting data is just another opinion_!"

I have some data!:upside_down_face:
(1) On cloudy days, the temperature gets up to around 35 to 38 degrees C.
(2) At night the enclosure cools down to around 14 deg C, depending on how cool the night is.
(3) On sunny days the temp gets up to 50 deg C at later times of the day such as 1700 local time.
(4) All of these cases are with *all* equipment running (except transmitters, which would only be on for very short periods anyway).

This means, the heat generated by the equipment itself is not causing the excessive temperatures.
The excessive heat is caused by sunlight impinging on the gray steel enclosure.

My immediate solution:
Other than replacing the enclosure with a larger SS box, which would cost somewhere around $1000, we could cover the enclosure with reflective insulated panels. I have an insulated reflective box right now that could go up to the roof at any time to confirm this idea. It is made from the material I propose we use. (edited)

Clarification:
I have an insulated reflective box that could *fit over* the groundstation enclosure.
This would just be for a test to confirm the idea.

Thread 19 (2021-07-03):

Add tuned cavity to reject adjacent RF noise

glennl, 2021-07-03:
* UHF tuned cavity
* Will need larger enclosure; See Issue #17.

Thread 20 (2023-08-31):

UPD Board: Add series RC to slow-start driver to improve slew rate

glennl, 2023-08-31:
There is an improvement to the slow-start circuit that provides better slew rate control. It is implemented by placing a series RC between the Gate and Drain. An example of values could be R=1k, C=0.47uF. Other existing components are unchanged except for possibly changing the existing capacitor to a smaller value, say 10 nF.

The following diagram illustrates this configuration. NB: It is just an example for clarity.
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

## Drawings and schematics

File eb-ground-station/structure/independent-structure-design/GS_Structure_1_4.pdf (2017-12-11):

# OreSat Ground Station

### EB Mast Structure www.oresat.org

V1.4 9-Dec-2017 pg. 1 of 2

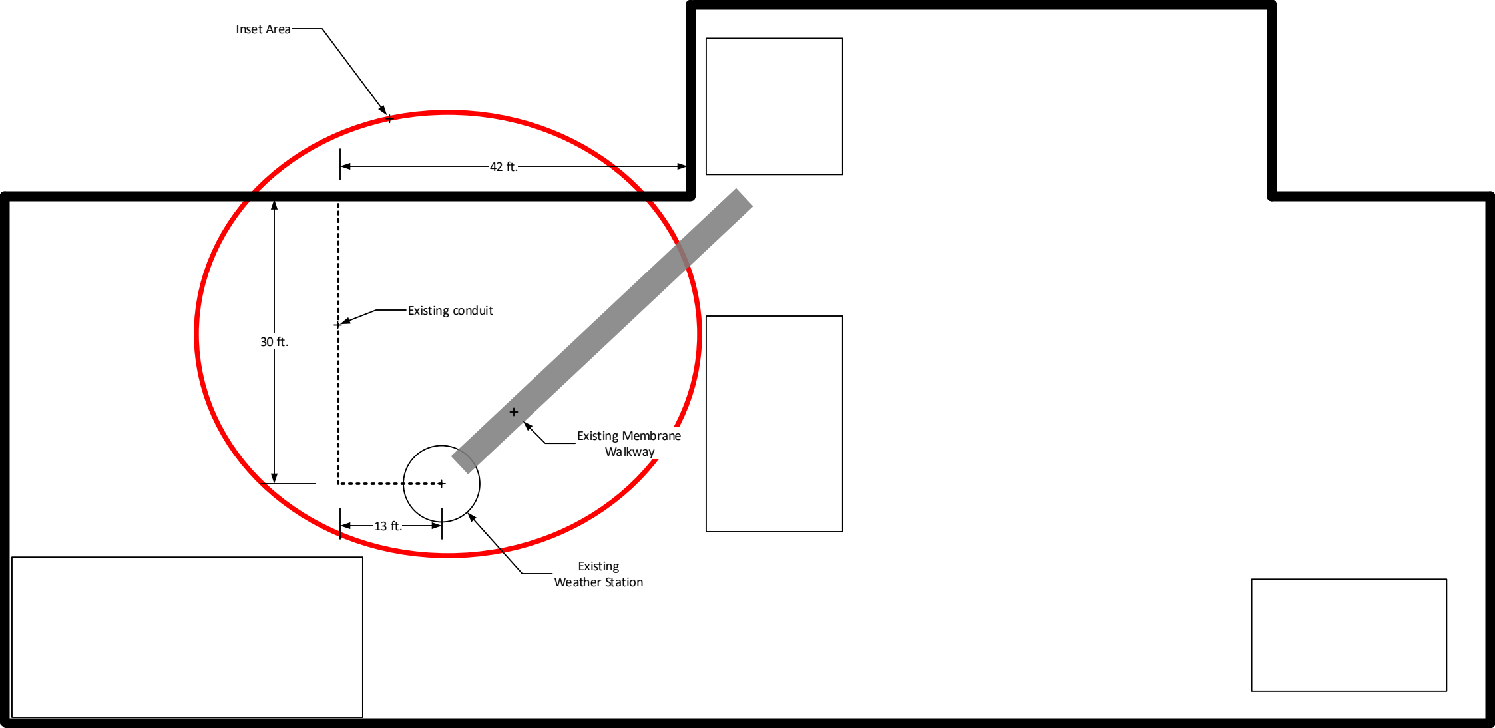
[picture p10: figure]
Existing Membrane Walkway; Existing Weather Station; Inset Area; Existing conduit

60 ft.

# Top Roof Level

## Plan view -- Not to scale

# Inset

## Plan view -- Not to scale

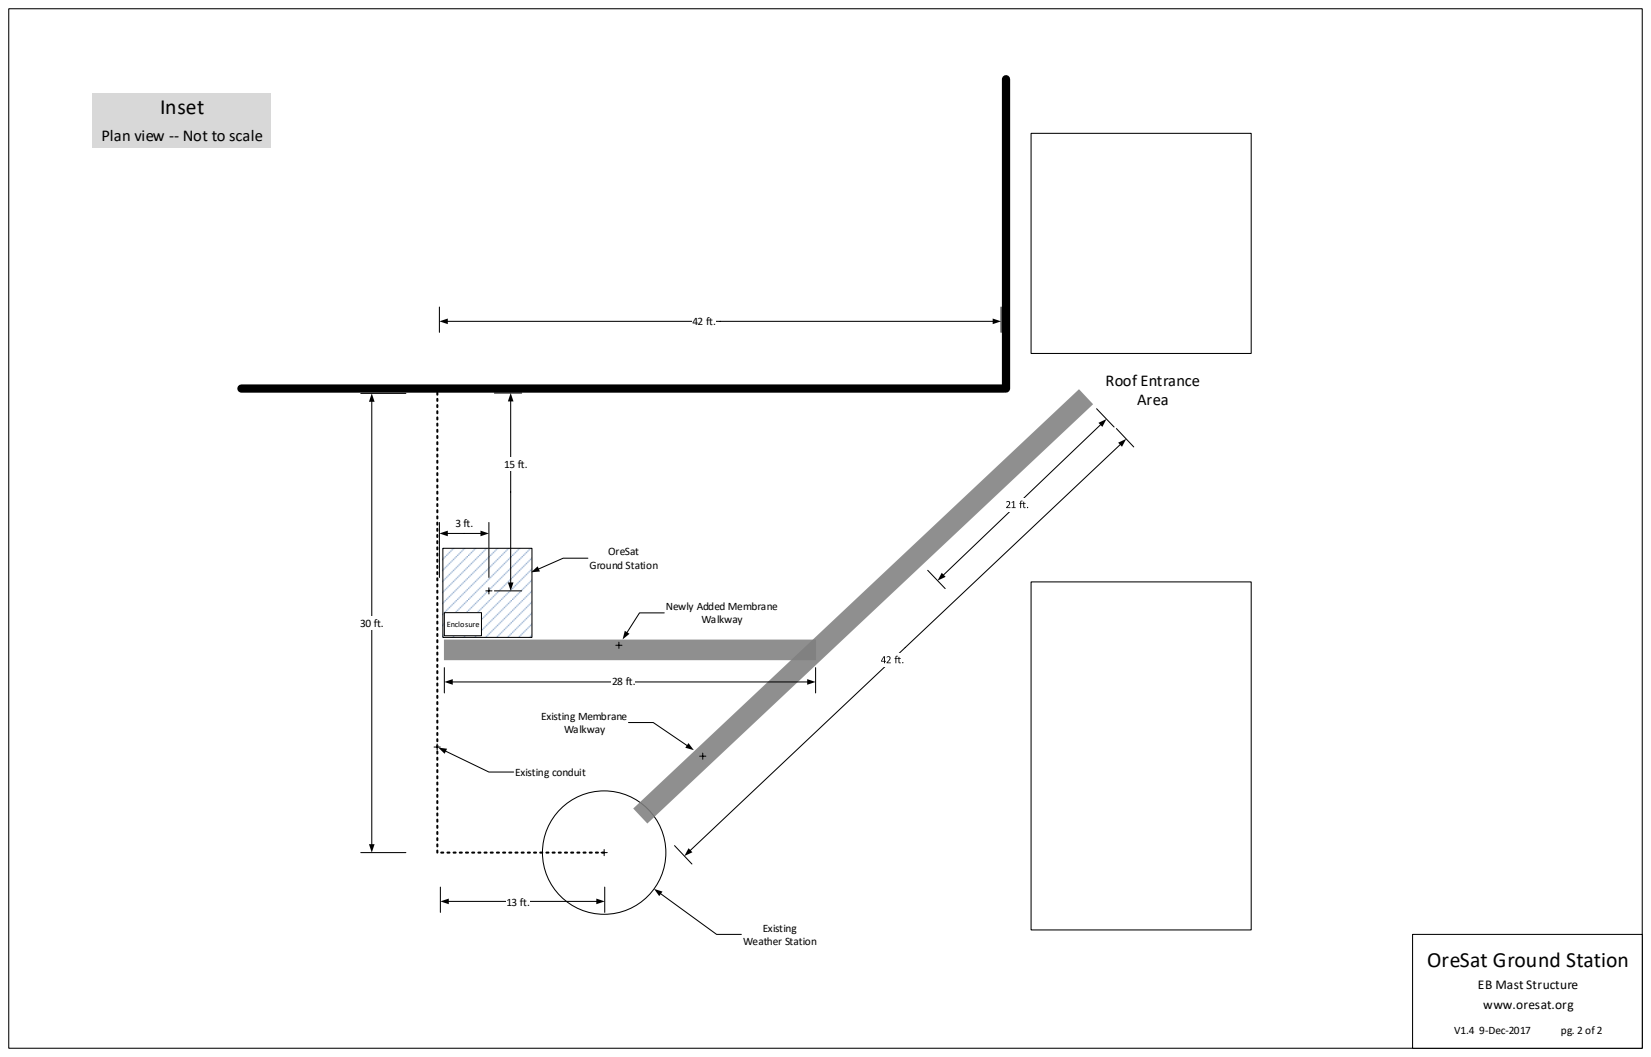
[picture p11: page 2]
V1.4 9-Dec-2017; Existing Membrane Walkway; Existing Weather Station; Walkway; OreSat Ground Station; Roof Entrance Area; Existing conduit; Enclosure

Newly Added Membrane

OreSat Ground Station

EB Mast Structure
www.oresat.org

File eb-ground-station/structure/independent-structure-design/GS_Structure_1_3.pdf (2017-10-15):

# OreSat Ground Station

### EB Mast Structure www.oresat.org

V1.3 14-Oct-2017 pg. 1 of 2

Existing Membrane Walkway; Existing Weather Station; Inset Area; Existing conduit

60 ft.

# Top Roof Level

## Plan view -- Not to scale

# Inset

## Plan view -- Not to scale

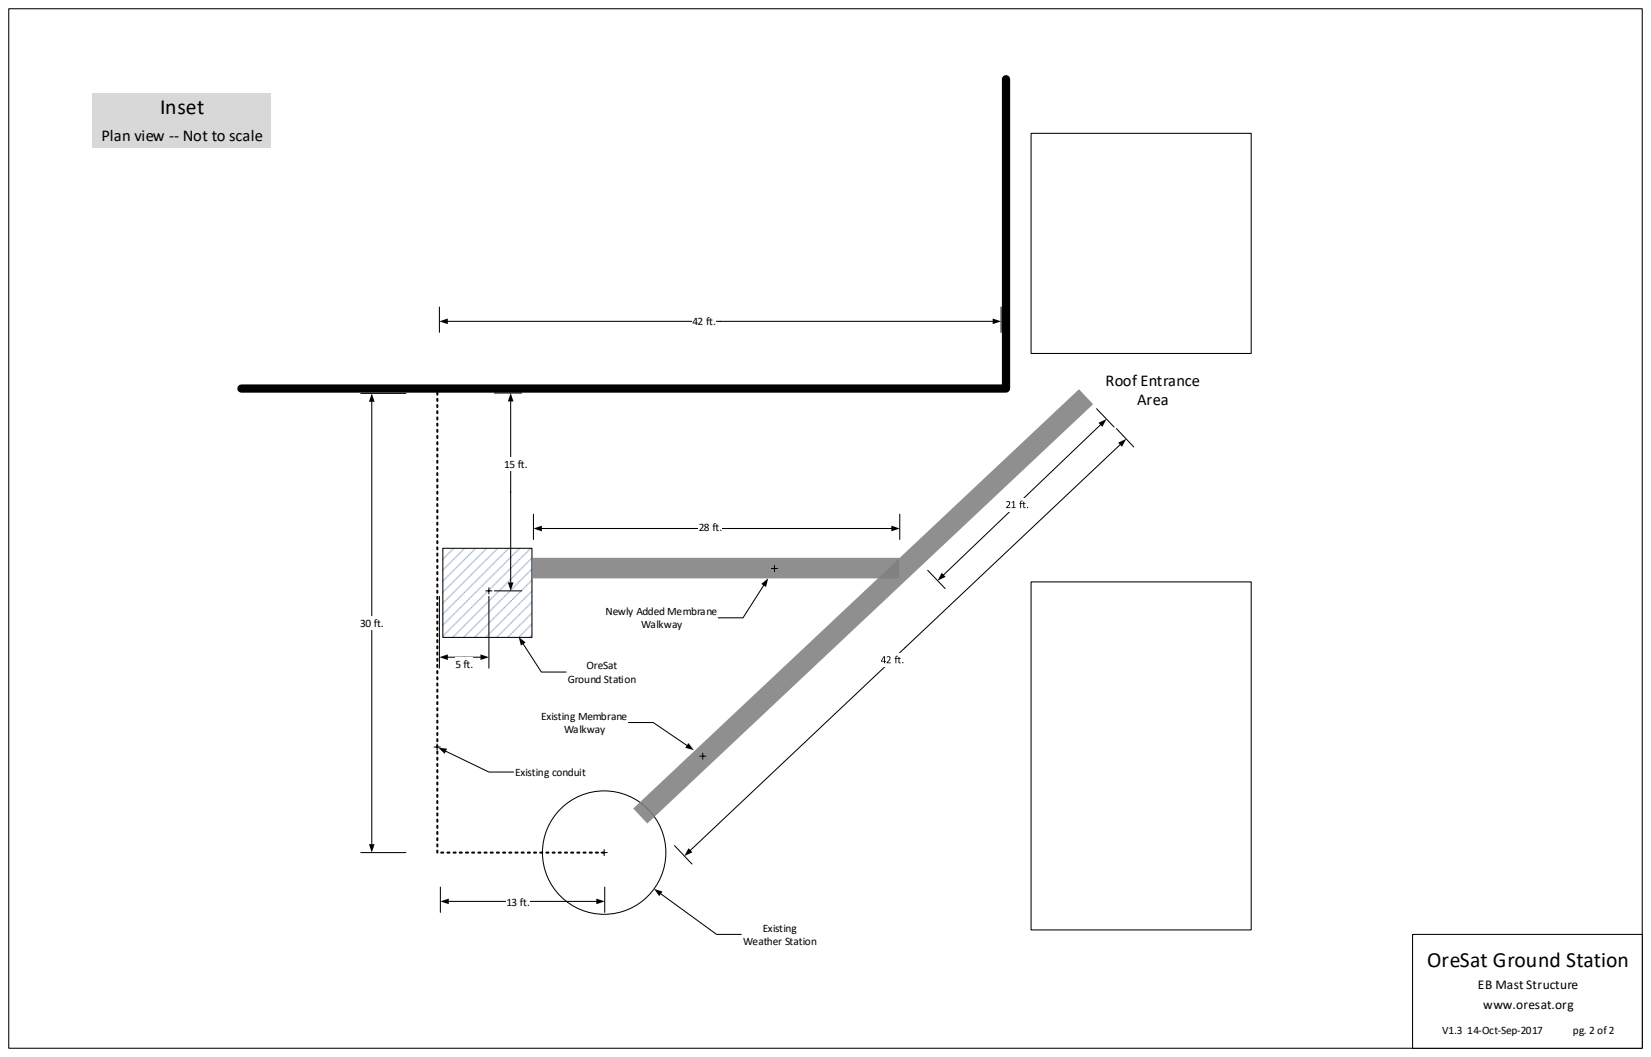
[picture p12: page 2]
V1.3 14-Oct-Sep-2017; Existing Membrane Walkway; Existing Weather Station; Walkway; OreSat Ground Station; Roof Entrance Area; Existing conduit

Newly Added Membrane

OreSat Ground Station

EB Mast Structure
www.oresat.org

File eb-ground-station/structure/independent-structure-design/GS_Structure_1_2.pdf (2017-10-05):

# OreSat Ground Station

### EB Mast Structure www.oresat.org

V1.0 29-Sep-2017 pg. 1 of 2

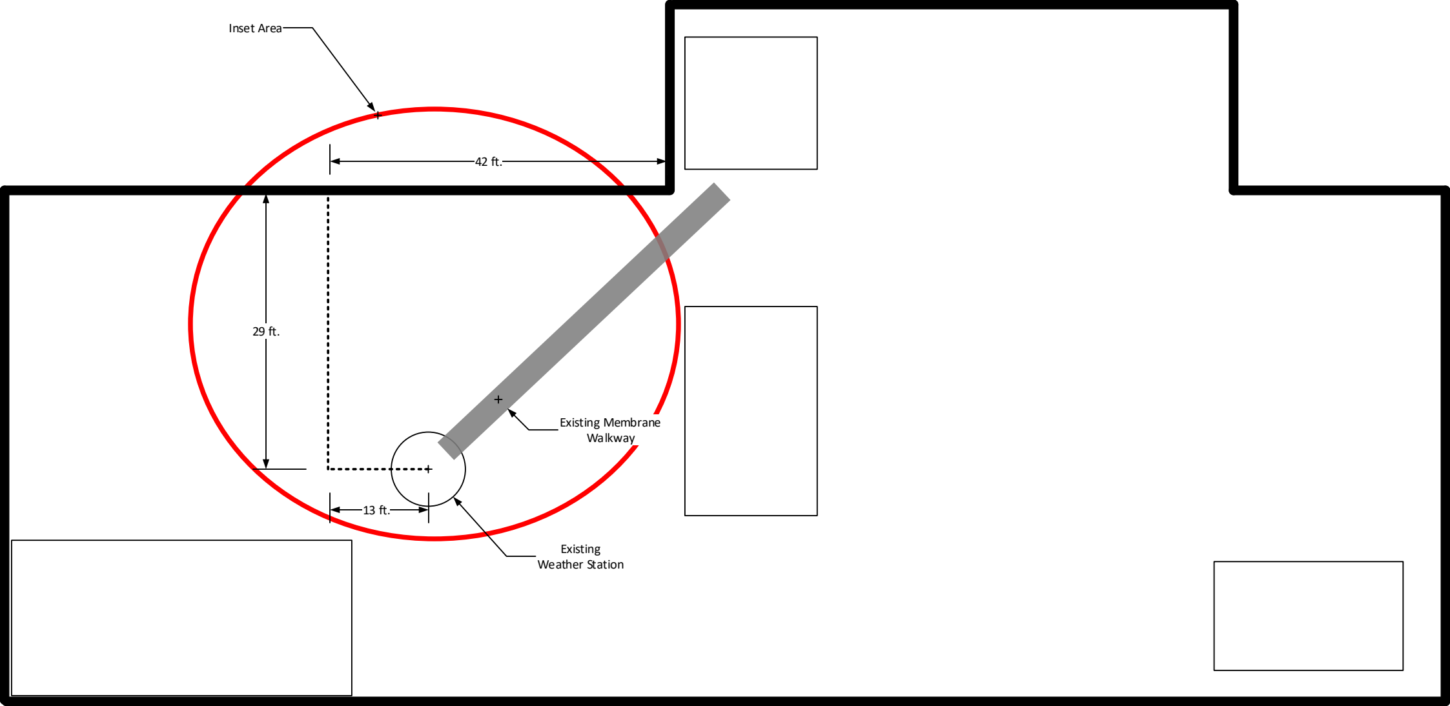
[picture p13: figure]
Existing Membrane Walkway; Existing Weather Station; Inset Area

60 ft.

# Top Roof Level

## Plan view -- Not to scale

# Inset

## Plan view -- Not to scale

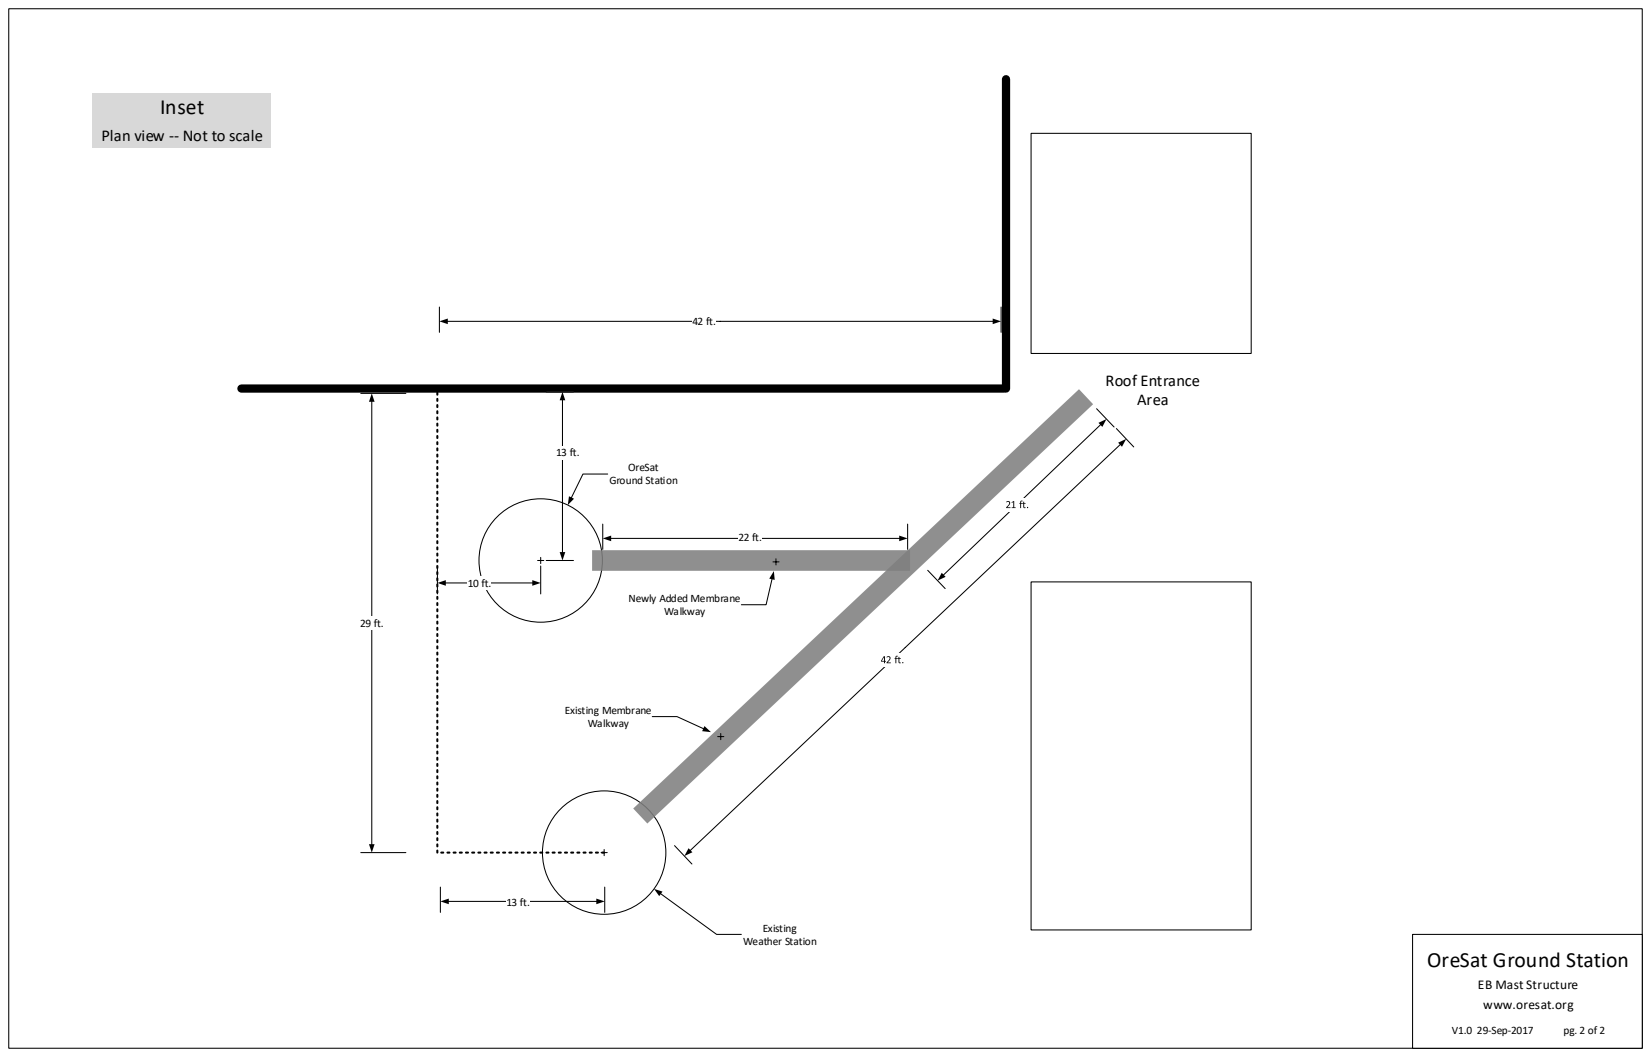
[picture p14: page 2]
V1.0 29-Sep-2017; Existing Membrane Walkway; Existing Weather Station; Walkway; OreSat Ground Station; Roof Entrance Area

Newly Added Membrane

OreSat Ground Station

EB Mast Structure
www.oresat.org

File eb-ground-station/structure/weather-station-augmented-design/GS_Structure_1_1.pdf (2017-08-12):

# Station Mast

## Plan view -- Not to scale

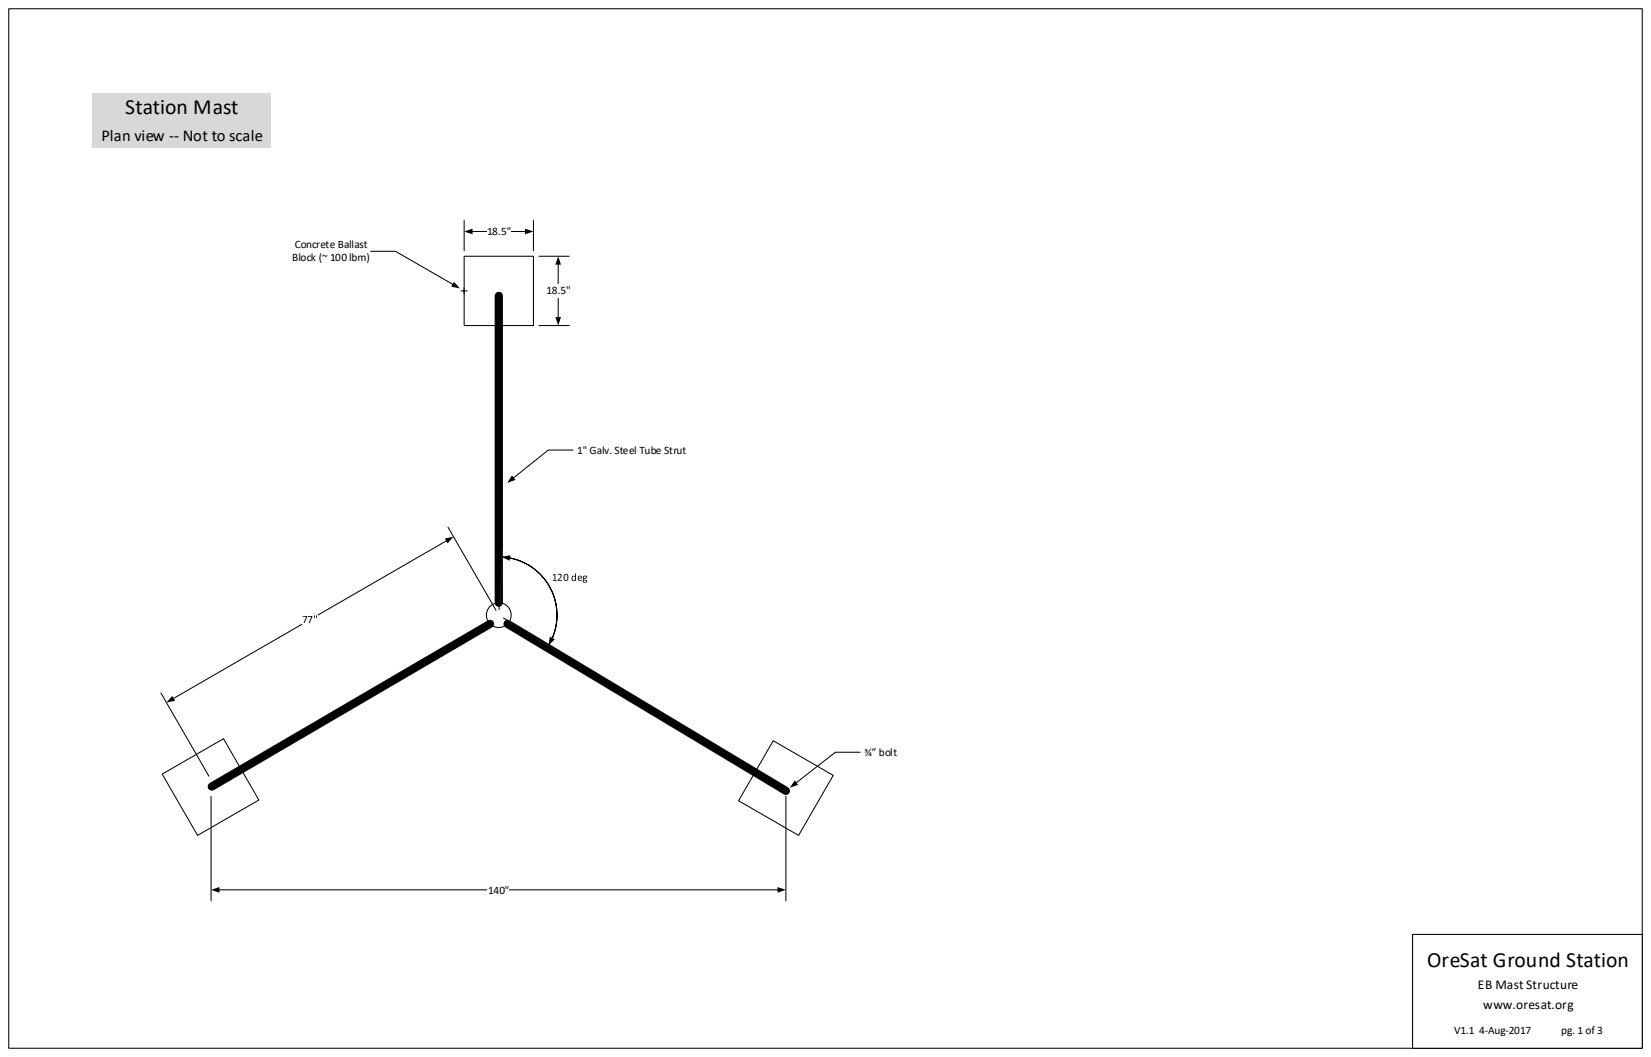
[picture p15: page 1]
V1.1 4-Aug-2017; Concrete Ballast Block (~ 100 lbm); ¾ bolt

1" Galv. Steel Tube Strut

OreSat Ground Station

EB Mast Structure
www.oresat.org

# Existing Station Mast

## Elevation view -- Not to scale

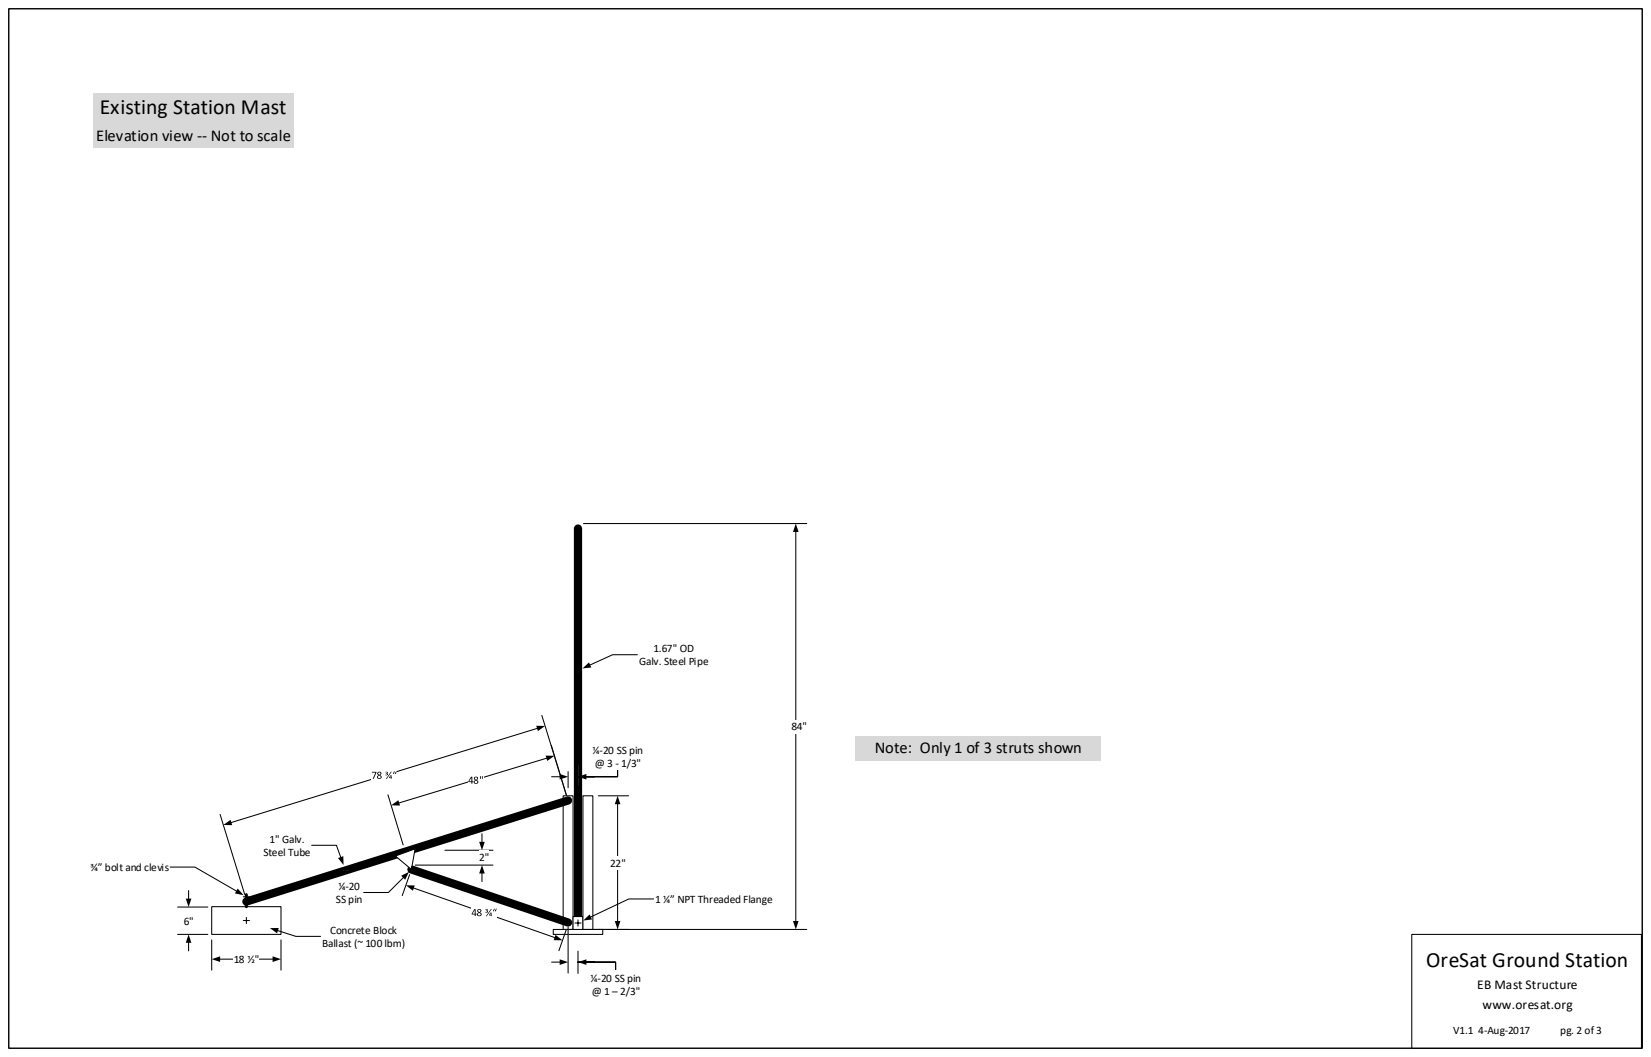
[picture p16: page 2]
¼-20 SS pin @ 1 – 2/3"; ¼-20 SS pin @ 3 - 1/3"; Concrete Block Ballast (~ 100 lbm); 1" Galv. Steel Tube; ¼-20 SS pin

Galv. Steel Pipe

Note: Only 1 of 3 struts shown

¾ bolt and clevis

1 ¼ NPT Threaded Flange

OreSat Ground Station

# Augmented Station Mast

## Elevation view -- Not to scale

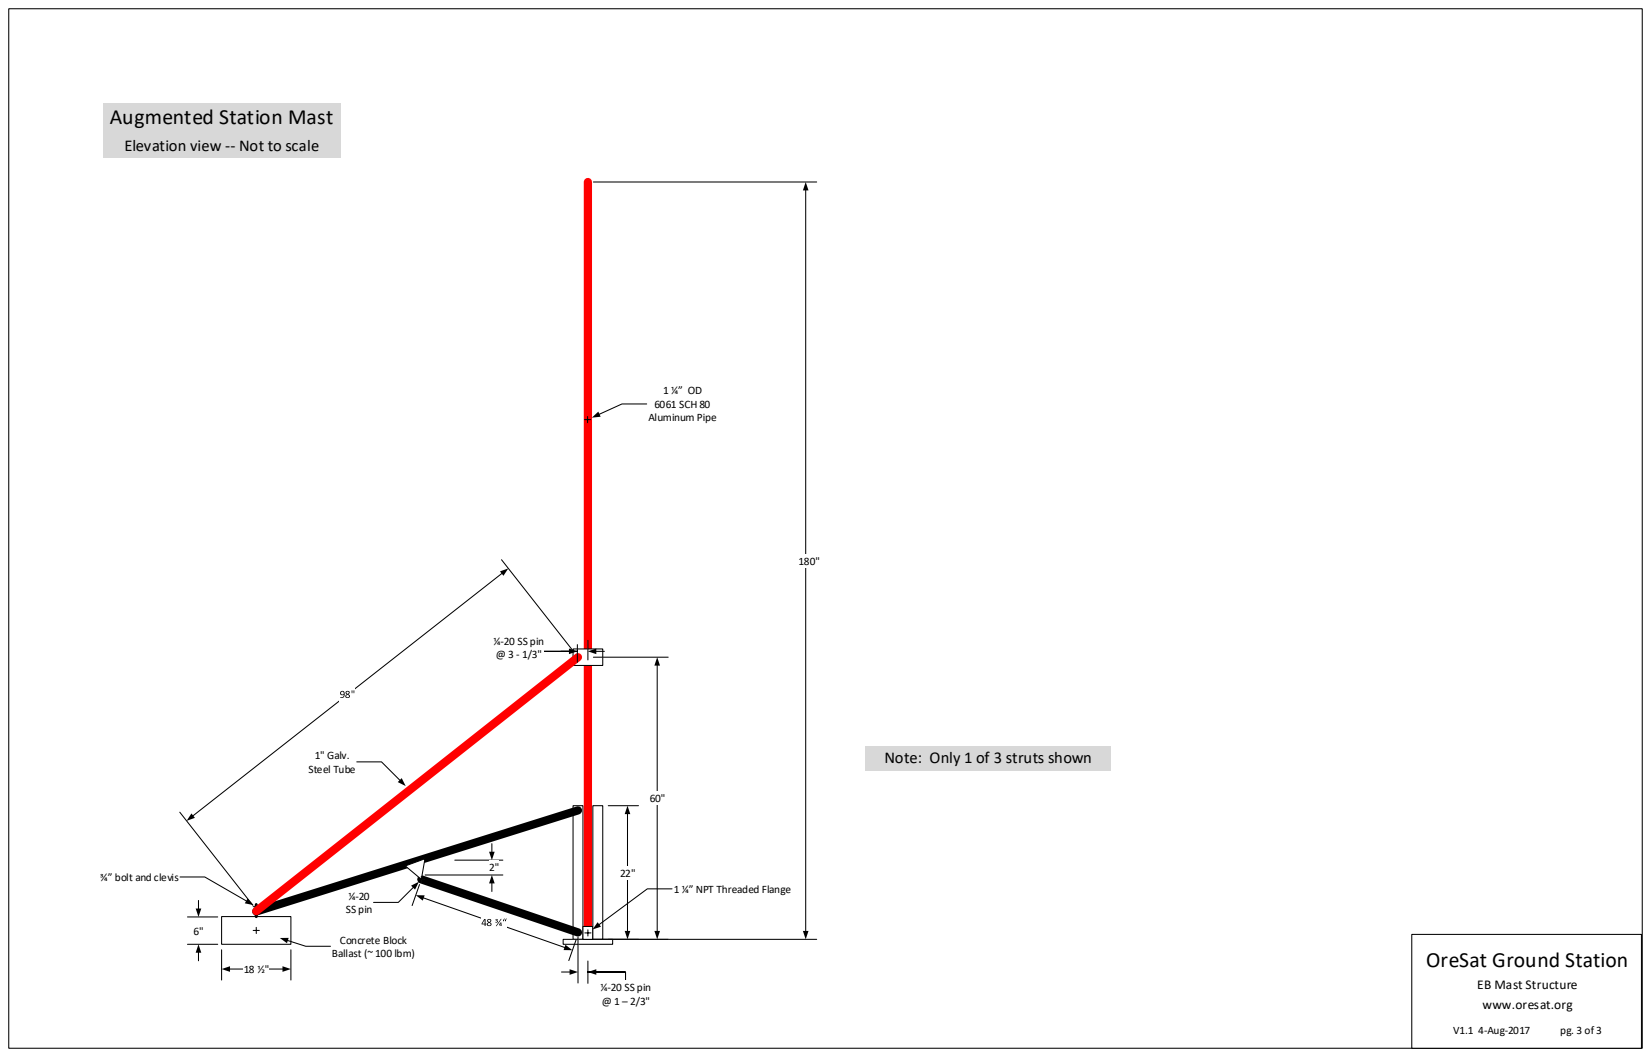
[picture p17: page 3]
¼-20 SS pin @ 1 – 2/3"; Concrete Block Ballast (~ 100 lbm); 1" Galv. Steel Tube; 1 ¼ OD 6061 SCH 80 Aluminum Pipe; ¼-20 SS pin; ¼-20 SS pin @ 3 - 1/3"

Note: Only 1 of 3 struts shown

¾ bolt and clevis

1 ¼ NPT Threaded Flange

OreSat Ground Station

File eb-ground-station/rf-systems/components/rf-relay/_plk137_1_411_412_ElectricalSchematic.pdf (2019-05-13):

411/412 | Electrical Schematics | DPDT

# 411C/412 Failsafe

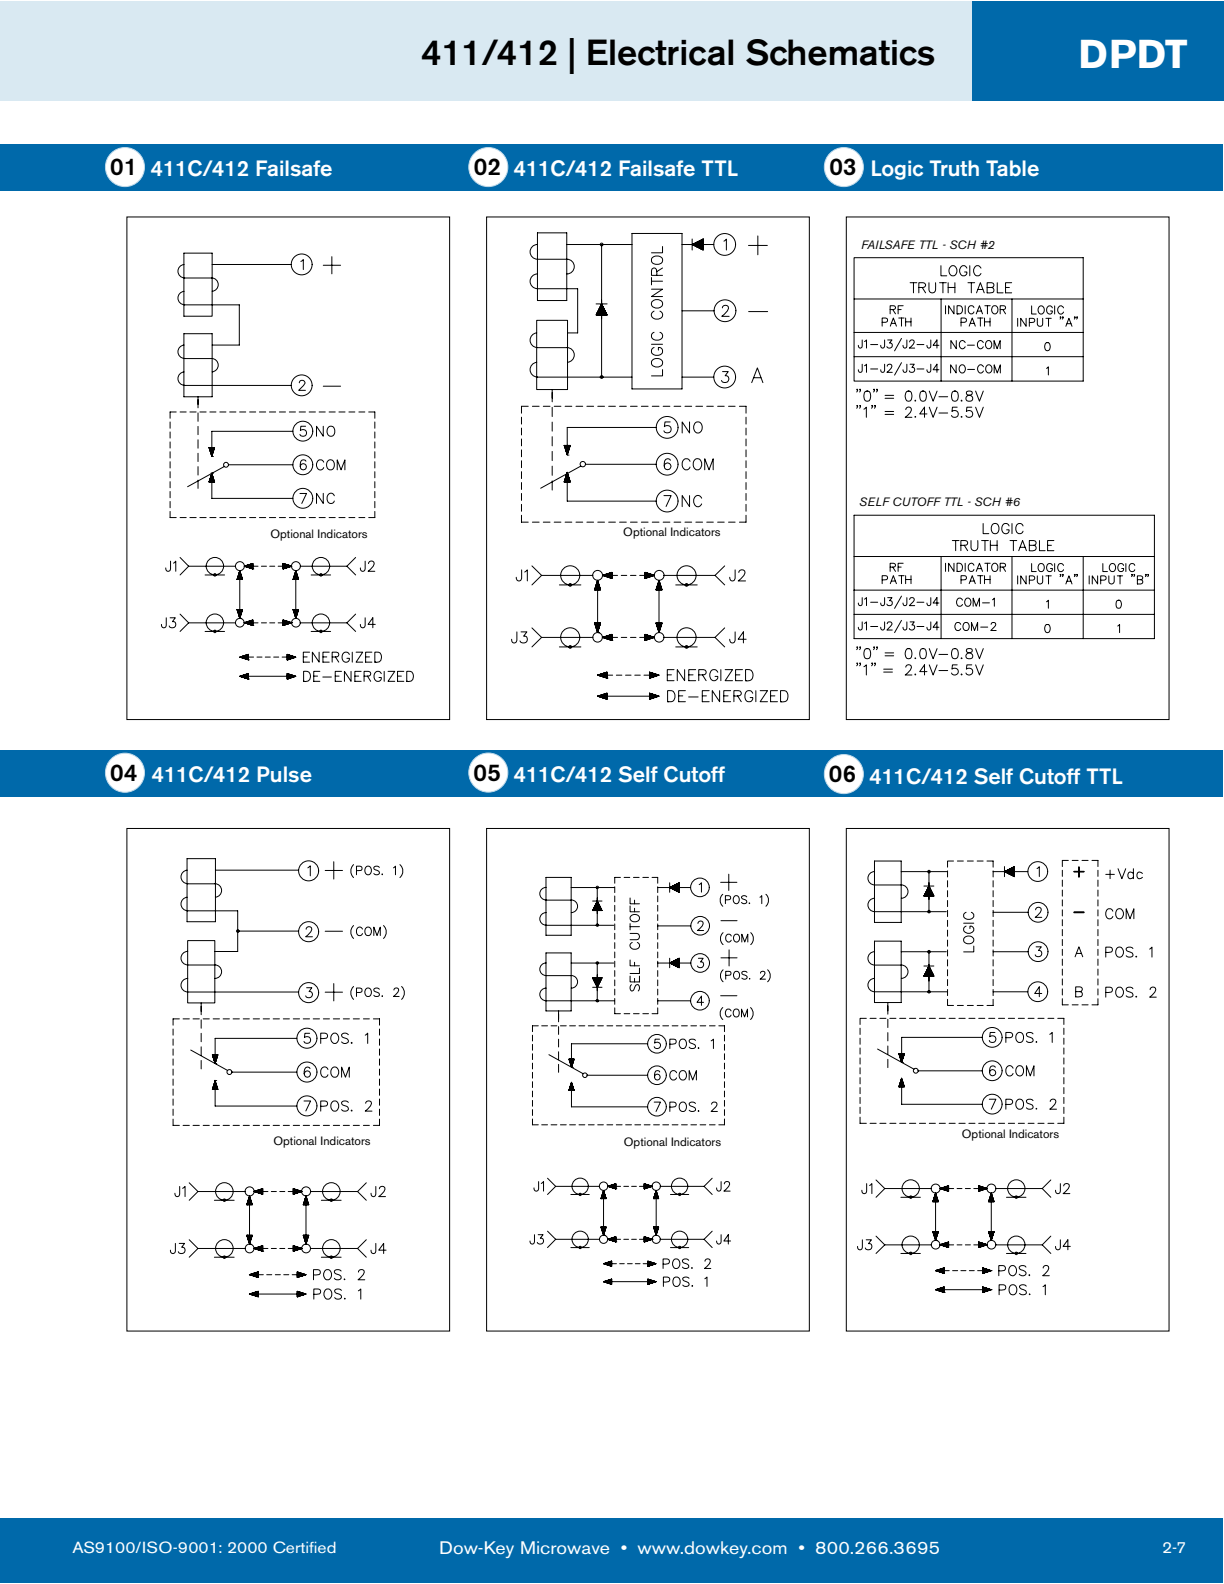
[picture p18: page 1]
Optional Indicators; AS9100/ISO-9001: 2000 Certified; Dow-Key Microwaveswww.dowkey.coms800.266.3695; 411C/412 Pulse; 411C/412 Failsafe TTL; 411C/412 Self Cutoff; 411C/412 Self Cutoff TTL; 03 Logic Truth Table

FAILSAFE TTL - SCH #2

SELF CUTOFF TTL - SCH #6

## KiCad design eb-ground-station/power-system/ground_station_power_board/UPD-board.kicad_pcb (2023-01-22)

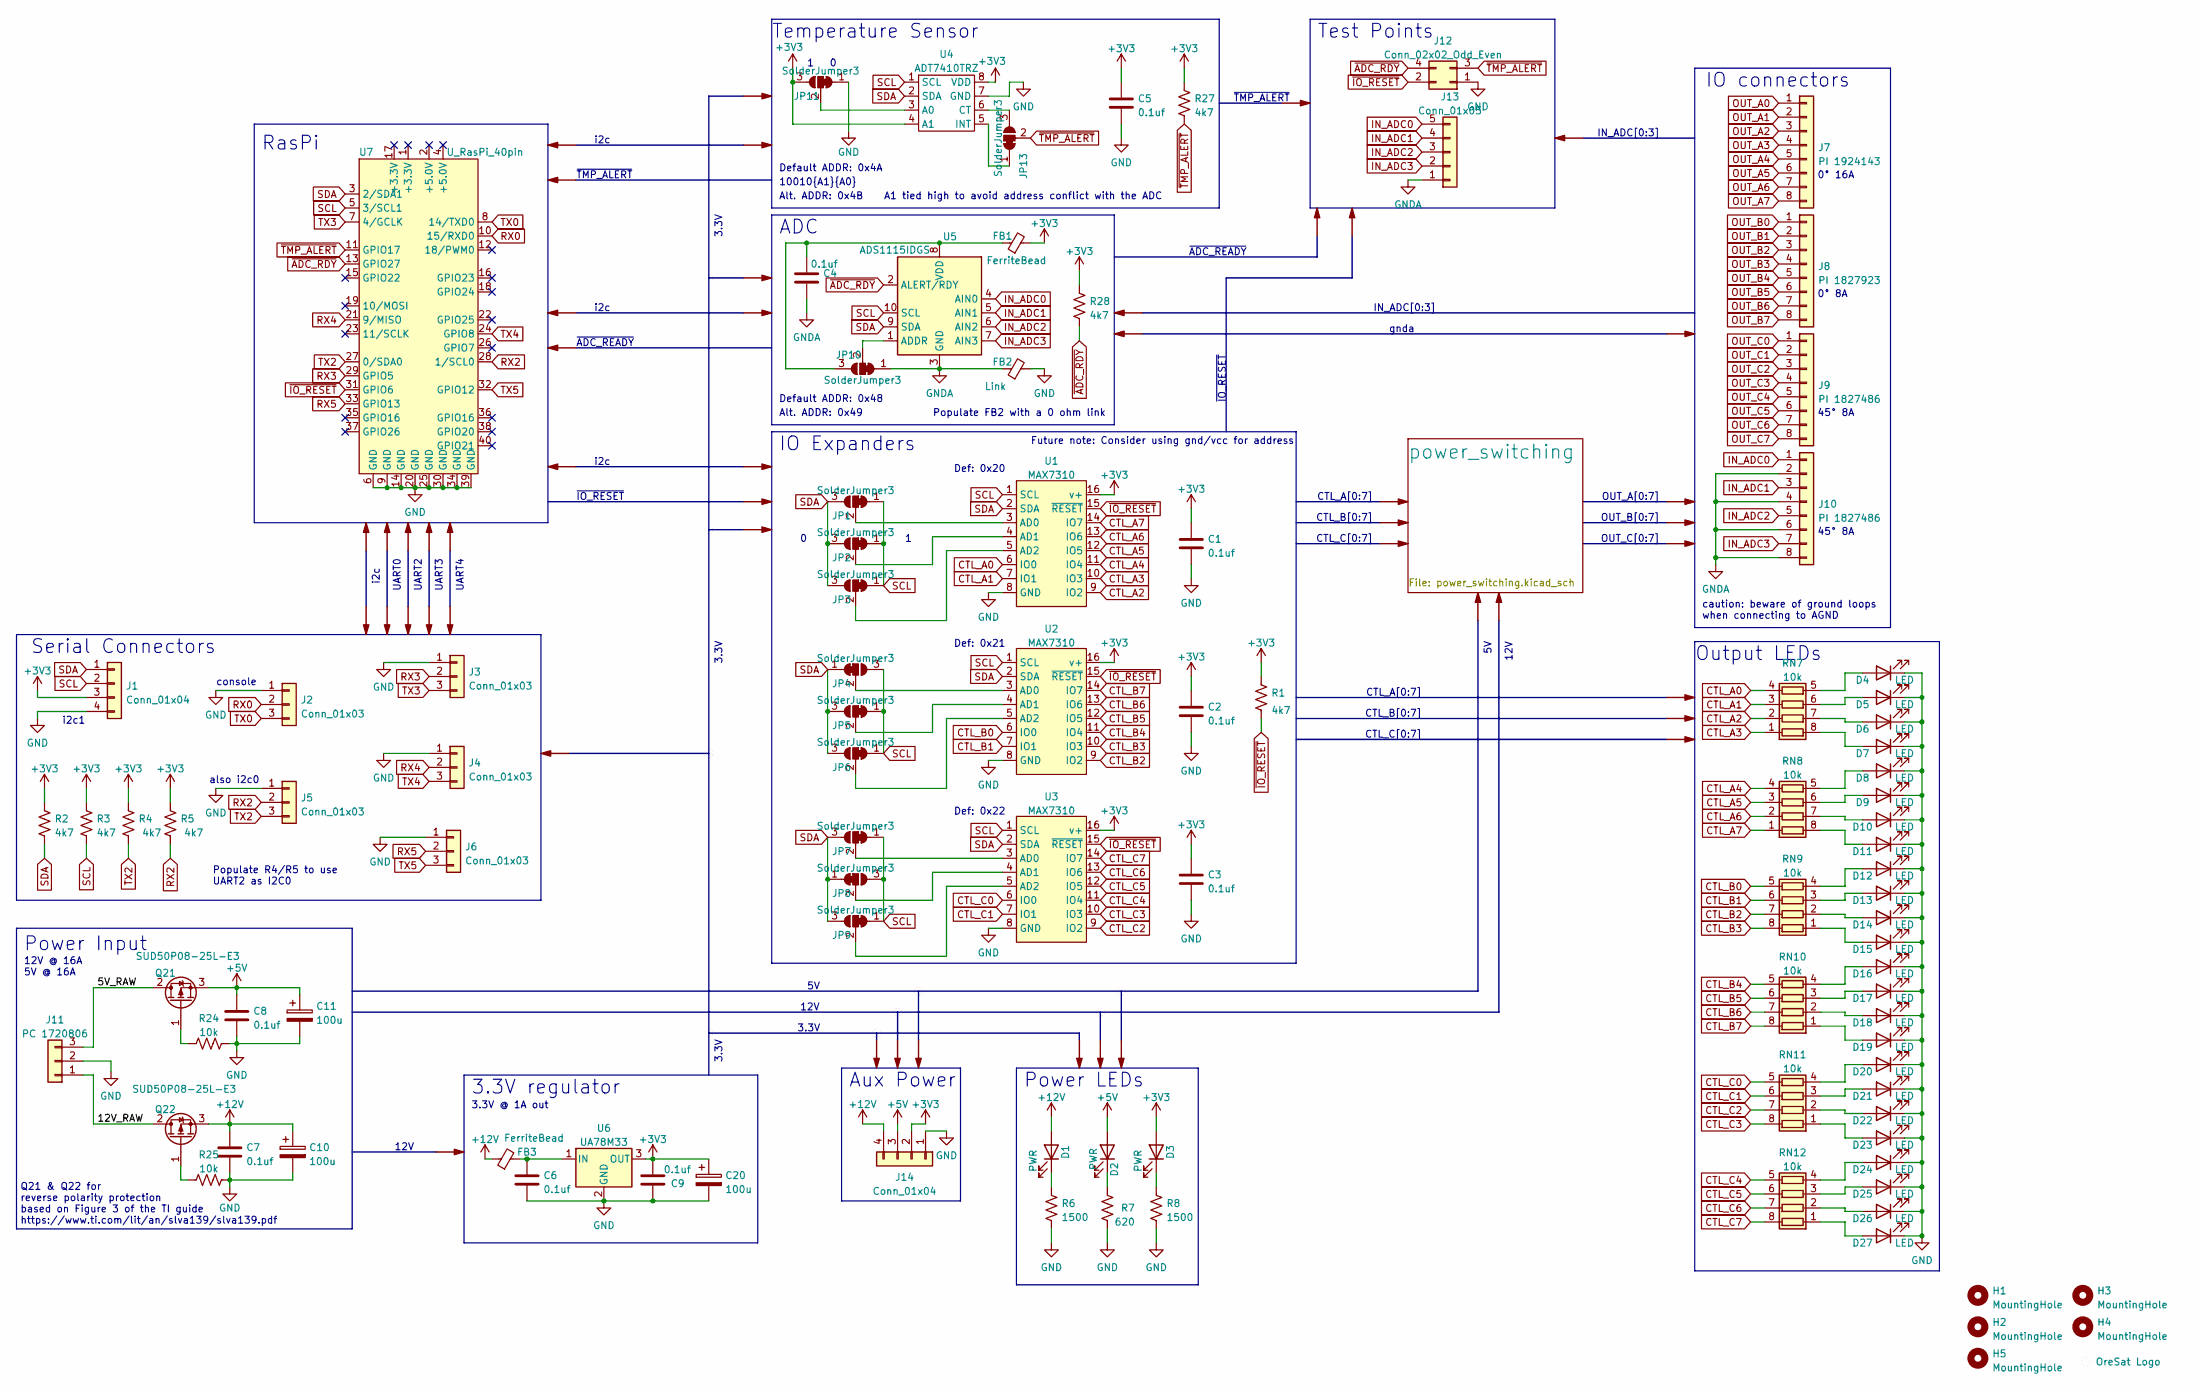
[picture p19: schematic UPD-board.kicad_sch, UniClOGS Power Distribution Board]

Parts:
C1, C2, C3, C4, C5, C6, C7, C8, C9: 0.1uf; C_0603_1608Metric; MPN CL10B104KB8NNWC
C10, C11, C20: 100u; CP_Elec_6.3x5.9; MPN 865080445010
D1, D2, D3: PWR; LED_0603_1608Metric
D4, D5, D6, D7, D8, D9, D10, D11, D12, D13, D14, D15, D16, D17, D18, D19, D20, D21, D22, D23, D24, D25, D26, D27: LED; LED_0603_1608Metric
FB1, FB3: FerriteBead; C_0805_2012Metric; MPN WLBD2012HCU310TH
FB2: Link; R_0805_2012Metric
H1, H2, H3, H4, H5: MountingHole; H-MCMASTER-94100A150
J1, J14: Conn_01x04; PinHeader_1x04_P2.54mm_Vertical
J2, J3, J4, J5, J6: Conn_01x03; PinHeader_1x03_P2.54mm_Vertical
J7: PI 1924143; J_PhoenixContact_MC_1,5_8-GF-5.08_1x08_P5.08mm_Horizontal_T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
J8: PI 1827923; PhoenixContact_MC_1,5_8-GF-3.81_1x08_P3.81mm_Horizontal_Thr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
J9, J10: PI 1827486; J_PhoenixContact_MC_1,5_8-GF-3.81_1x08_P3.81mm_45degree_Thr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
J11: PC 1720806; PhoenixContact_GMSTBA_2,5_3-G-7,62_1x03_P7.62mm_Horizontal
J12: Conn_02x02_Odd_Even; PinHeader_2x02_P2.54mm_Vertical
J13: Conn_01x05; PinHeader_1x05_P2.54mm_Vertical
JP1, JP2, JP3, JP4, JP5, JP6, JP7, JP8, JP9, JP10, JP11, JP13: SolderJumper3; SolderJumper-3_P1.3mm_Bridged12_Pad1.0x1.5mm
LOGO1: OreSat Logo; logo-small
Q21, Q22: SUD50P08-25L-E3; TO-252-3_TabIsPin2
R1, R2, R3, R4, R5, R27, R28: 4k7; R_0603_1608Metric
R6, R8: 1500; R_0603_1608Metric
R7: 620; R_0603_1608Metric
R24, R25: 10k; R_0603_1608Metric
RN7, RN8, RN9, RN10, RN11, RN12: 10k; R_Array_Convex_4x0603; MPN RAVF164DJT10K0
U1, U2, U3: MAX7310; TSSOP-16_4.4x5mm_P0.65mm; MPN MAX7310ATE+T
U4: ADT7410TRZ; SOIC-8_3.9x4.9mm_P1.27mm
U5: ADS1115IDGS; TSSOP-10_3x3mm_P0.5mm
U6: UA78M33; SOT-223-3_TabPin2
U7: U_RasPi_40pin; IDC-Header_2x20_P2.54mm_Vertical

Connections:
+3V3: C1.1, C2.1, C3.1, C5.1, C9.1, C20.1, D3.2 (A), FB1.2, J1.3, J14.2, JP11.3 (B), R1.1, R2.1, R3.1, R4.1, R5.1, R27.1, R28.1, U1.16 (v+), U2.16 (v+), U3.16 (v+), U4.4 (A1), U4.8 (VDD), U6.3 (OUT); also elsewhere on the board
+5V: C8.2, C11.1, D2.2 (A), J14.3, Q21.3 (S); also elsewhere on the board
+12V: C7.1, C10.1, D1.2 (A), FB3.1, J14.4, Q22.3 (S); also elsewhere on the board
/5V_RAW: J11.3, Q21.2 (D)
/12V_RAW: J11.1, Q22.2 (D)
CTL_A0: RN7.4 (R4.1), U1.6 (IO0); also elsewhere on the board
CTL_A1: RN7.3 (R3.1), U1.7 (IO1); also elsewhere on the board
CTL_A2: RN7.2 (R2.1), U1.9 (IO2); also elsewhere on the board
CTL_A3: RN7.1 (R1.1), U1.10 (IO3); also elsewhere on the board
CTL_A4: RN8.4 (R4.1), U1.11 (IO4); also elsewhere on the board
CTL_A5: RN8.3 (R3.1), U1.12 (IO5); also elsewhere on the board
CTL_A6: RN8.2 (R2.1), U1.13 (IO6); also elsewhere on the board
CTL_A7: RN8.1 (R1.1), U1.14 (IO7); also elsewhere on the board
CTL_B0: RN9.5 (R4.2), U2.6 (IO0); also elsewhere on the board
CTL_B1: RN9.6 (R3.2), U2.7 (IO1); also elsewhere on the board
CTL_B2: RN9.7 (R2.2), U2.9 (IO2); also elsewhere on the board
CTL_B3: RN9.8 (R1.2), U2.10 (IO3); also elsewhere on the board
CTL_B4: RN10.5 (R4.2), U2.11 (IO4); also elsewhere on the board
CTL_B5: RN10.6 (R3.2), U2.12 (IO5); also elsewhere on the board
CTL_B6: RN10.7 (R2.2), U2.13 (IO6); also elsewhere on the board
CTL_B7: RN10.8 (R1.2), U2.14 (IO7); also elsewhere on the board
CTL_C0: RN11.5 (R4.2), U3.6 (IO0); also elsewhere on the board
CTL_C1: RN11.6 (R3.2), U3.7 (IO1); also elsewhere on the board
CTL_C2: RN11.7 (R2.2), U3.9 (IO2); also elsewhere on the board
CTL_C3: RN11.8 (R1.2), U3.10 (IO3); also elsewhere on the board
CTL_C4: RN12.5 (R4.2), U3.11 (IO4); also elsewhere on the board
CTL_C5: RN12.6 (R3.2), U3.12 (IO5); also elsewhere on the board
CTL_C6: RN12.7 (R2.2), U3.13 (IO6); also elsewhere on the board
CTL_C7: RN12.8 (R1.2), U3.14 (IO7); also elsewhere on the board
GND: C1.2, C2.2, C3.2, C5.2, C6.2, C7.2, C8.1, C9.2, C10.2, C11.2, C20.2, D4.1 (K), D5.1 (K), D6.1 (K), D7.1 (K), D8.1 (K), D9.1 (K), D10.1 (K), D11.1 (K), D12.1 (K), D13.1 (K), D14.1 (K), D15.1 (K), D16.1 (K), D17.1 (K), D18.1 (K), D19.1 (K), D20.1 (K), D21.1 (K), D22.1 (K), D23.1 (K), D24.1 (K), D25.1 (K), D26.1 (K), D27.1 (K), FB2.2, J1.4, J2.1, J3.1, J4.1, J5.1, J6.1, J11.2, J12.1, J14.1, JP11.1 (A), R6.1, R7.2, R8.1, R24.1, R25.1, U1.8 (GND), U2.8 (GND), U3.8 (GND), U4.7 (GND), U6.2 (GND), U7.6 (GND), U7.9 (GND), U7.14 (GND), U7.20 (GND), U7.25 (GND), U7.30 (GND), U7.34 (GND), U7.39 (GND); also elsewhere on the board
GNDA: C4.2, FB2.1, J10.2, J10.4, J10.6, J10.8, J13.1, JP10.1 (A), U5.3 (GND)
IN_ADC0: J10.1, J13.5, U5.4 (AIN0)
IN_ADC1: J10.3, J13.4, U5.5 (AIN1)
IN_ADC2: J10.5, J13.3, U5.6 (AIN2)
IN_ADC3: J10.7, J13.2, U5.7 (AIN3)
unnamed: C4.1, FB1.1, JP10.3 (B), U5.8 (VDD)
unnamed: C6.1, FB3.2, U6.1 (IN)
unnamed: D1.1 (K), R6.2
unnamed: D2.1 (K), R7.1
unnamed: D3.1 (K), R8.2
unnamed: D4.2 (A), RN7.5 (R4.2)
unnamed: D5.2 (A), RN7.6 (R3.2)
unnamed: D6.2 (A), RN7.7 (R2.2)
unnamed: D7.2 (A), RN7.8 (R1.2)
unnamed: D8.2 (A), RN8.5 (R4.2)
unnamed: D9.2 (A), RN8.6 (R3.2)
unnamed: D10.2 (A), RN8.7 (R2.2)
unnamed: D11.2 (A), RN8.8 (R1.2)
unnamed: D12.2 (A), RN9.4 (R4.1)
unnamed: D13.2 (A), RN9.3 (R3.1)
unnamed: D14.2 (A), RN9.2 (R2.1)
unnamed: D15.2 (A), RN9.1 (R1.1)
unnamed: D16.2 (A), RN10.4 (R4.1)
unnamed: D17.2 (A), RN10.3 (R3.1)
unnamed: D18.2 (A), RN10.2 (R2.1)
unnamed: D19.2 (A), RN10.1 (R1.1)
unnamed: D20.2 (A), RN11.4 (R4.1)
unnamed: D21.2 (A), RN11.3 (R3.1)
unnamed: D22.2 (A), RN11.2 (R2.1)
unnamed: D23.2 (A), RN11.1 (R1.1)
unnamed: D24.2 (A), RN12.4 (R4.1)
unnamed: D25.2 (A), RN12.3 (R3.1)
unnamed: D26.2 (A), RN12.2 (R2.1)
unnamed: D27.2 (A), RN12.1 (R1.1)
unnamed: JP1.2 (C), U1.3 (AD0)
unnamed: JP2.2 (C), U1.4 (AD1)
unnamed: JP3.2 (C), U1.5 (AD2)
unnamed: JP4.2 (C), U2.3 (AD0)
unnamed: JP5.2 (C), U2.4 (AD1)
unnamed: JP6.2 (C), U2.5 (AD2)
unnamed: JP7.2 (C), U3.3 (AD0)
unnamed: JP8.2 (C), U3.4 (AD1)
unnamed: JP9.2 (C), U3.5 (AD2)
unnamed: JP10.2 (C), U5.1 (ADDR)
unnamed: JP11.2 (C), U4.3 (A0)
unnamed: JP13.1 (A), U4.5 (INT)
unnamed: JP13.3 (B), U4.6 (CT)
unnamed: Q21.1 (G), R24.2
unnamed: Q22.1 (G), R25.2
OUT_A0: J7.1; also elsewhere on the board
OUT_A1: J7.2; also elsewhere on the board
OUT_A2: J7.3; also elsewhere on the board
OUT_A3: J7.4; also elsewhere on the board
OUT_A4: J7.5; also elsewhere on the board
OUT_A5: J7.6; also elsewhere on the board
OUT_A6: J7.7; also elsewhere on the board
OUT_A7: J7.8; also elsewhere on the board
OUT_B0: J8.1; also elsewhere on the board
OUT_B1: J8.2; also elsewhere on the board
OUT_B2: J8.3; also elsewhere on the board
OUT_B3: J8.4; also elsewhere on the board
OUT_B4: J8.5; also elsewhere on the board
OUT_B5: J8.6; also elsewhere on the board
OUT_B6: J8.7; also elsewhere on the board
OUT_B7: J8.8; also elsewhere on the board
OUT_C0: J9.1; also elsewhere on the board
OUT_C1: J9.2; also elsewhere on the board
OUT_C2: J9.3; also elsewhere on the board
OUT_C3: J9.4; also elsewhere on the board
OUT_C4: J9.5; also elsewhere on the board
OUT_C5: J9.6; also elsewhere on the board
OUT_C6: J9.7; also elsewhere on the board
OUT_C7: J9.8; also elsewhere on the board
RX0: J2.2, U7.10 (15/RXD0)
RX2: J5.2, R5.2, U7.28 (1/SCL0)
RX3: J3.2, U7.29 (GPIO5)
RX4: J4.2, U7.21 (9/MISO)
RX5: J6.2, U7.33 (GPIO13)
SCL: J1.2, JP1.1 (A), JP2.1 (A), JP3.1 (A), JP4.3 (B), JP5.1 (A), JP6.1 (A), JP7.1 (A), JP8.3 (B), JP9.1 (A), R3.2, U1.1 (SCL), U2.1 (SCL), U3.1 (SCL), U4.1 (SCL), U5.10 (SCL), U7.5 (3/SCL1)
SDA: J1.1, JP1.3 (B), JP2.3 (B), JP3.3 (B), JP4.1 (A), JP5.3 (B), JP6.3 (B), JP7.3 (B), JP8.1 (A), JP9.3 (B), R2.2, U1.2 (SDA), U2.2 (SDA), U3.2 (SDA), U4.2 (SDA), U5.9 (SDA), U7.3 (2/SDA1)
TX0: J2.3, U7.8 (14/TXD0)
TX2: J5.3, R4.2, U7.27 (0/SDA0)
TX3: J3.3, U7.7 (4/GCLK)
TX4: J4.3, U7.24 (GPIO8)
TX5: J6.3, U7.32 (GPIO12)
~ADC_RDY: J12.4, R28.2, U5.2 (ALERT/RDY), U7.13 (GPIO27)
~IO_RESET: J12.2, R1.2, U1.15 (~RESET), U2.15 (~RESET), U3.15 (~RESET), U7.31 (GPIO6)
~TMP_ALERT: J12.3, JP13.2 (C), R27.2, U7.11 (GPIO17)

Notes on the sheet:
12V
UART4
OUT_A[0:7]
~{ADC_READY}
3.3V
Power Input
UART2
45° 8A
Test Points
Alt. ADDR: 0x4B
Def: 0x20
3.3V @ 1A out
OUT_C[0:7]
Serial Connectors
OUT_B[0:7]
Def: 0x21
0° 16A
also i2c0
CTL_A[0:7]
Def: 0x22
CTL_C[0:7]
Temperature Sensor
CTL_B[0:7]
UART0
12V @ 16A 5V @ 16A
caution: beware of ground loops when connecting to AGND
IN_ADC[0:3]
0° 8A
A1 tied high to avoid address conflict with the ADC
Alt. ADDR: 0x49
Output LEDs
~{TMP_ALERT}
RasPi
i2c
Aux Power
Populate R4/R5 to use UART2 as I2C0
Default ADDR: 0x48
IO connectors
Power LEDs
~{IO_RESET}

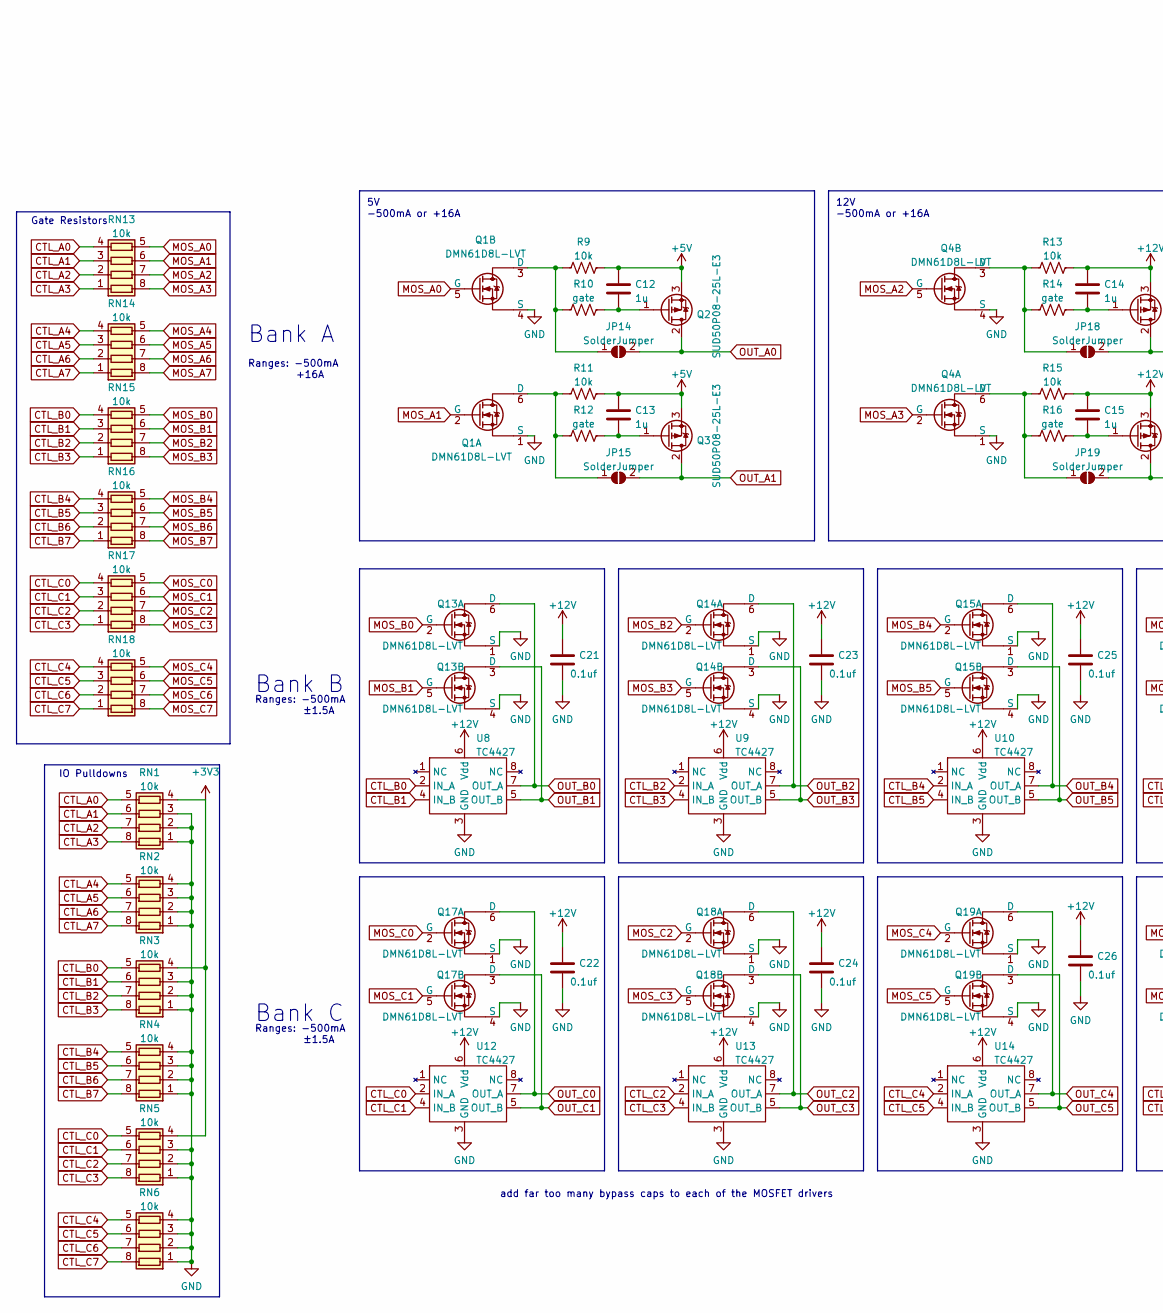
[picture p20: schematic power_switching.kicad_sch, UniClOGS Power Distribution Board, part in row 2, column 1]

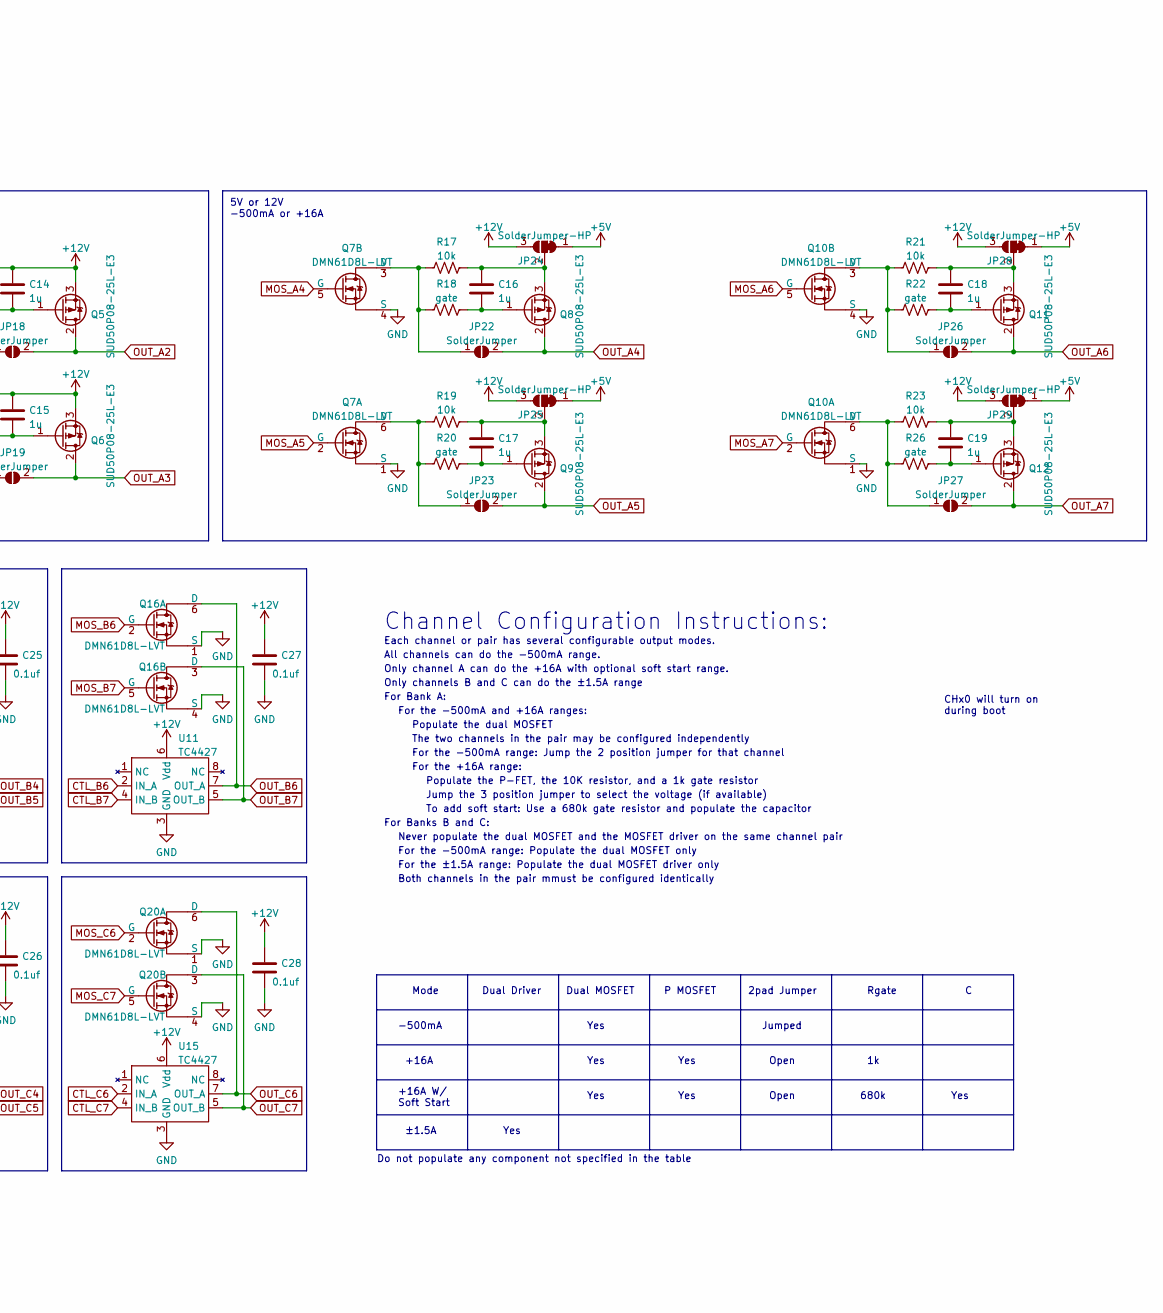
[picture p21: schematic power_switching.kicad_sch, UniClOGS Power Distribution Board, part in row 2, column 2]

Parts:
C12, C13, C14, C15, C16, C17, C18, C19: 1u; C_0603_1608Metric; MPN CL10B105KA8NNNC
C21, C22, C23, C24, C25, C26, C27, C28: 0.1uf; C_0603_1608Metric; MPN CL10B104KB8NNWC
JP14, JP15, JP18, JP19, JP22, JP23, JP26, JP27: SolderJumper; SolderJumper-2_P1.3mm_Open_RoundedPad1.0x1.5mm
JP24, JP25, JP28, JP29: SolderJumper-HP; JP-SOLDER-2way-HP
Q1, Q4, Q7, Q10, Q13, Q14, Q15, Q16, Q17, Q18, Q19, Q20: DMN61D8L-LVT; TSOT26-6
Q2, Q3, Q5, Q6, Q8, Q9, Q11, Q12: SUD50P08-25L-E3; TO-252-3_TabIsPin2
R9, R11, R13, R15, R17, R19, R21, R23: 10k; R_0603_1608Metric
R10, R12, R14, R16, R18, R20, R22, R26: gate; R_0603_1608Metric
RN1, RN2, RN3, RN4, RN5, RN6, RN13, RN14, RN15, RN16, RN17, RN18: 10k; R_Array_Convex_4x0603; MPN RAVF164DJT10K0
U8, U9, U10, U11, U12, U13, U14, U15: TC4427; MSOP-8_3x3mm_P0.65mm

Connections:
+3V3: RN1.4 (R4.1), RN3.4 (R4.1), RN5.4 (R4.1); also elsewhere on the board
+5V: C12.1, C13.1, JP24.1 (A), JP25.1 (A), JP28.1 (A), JP29.1 (A), Q2.3 (S), Q3.3 (S), R9.2, R11.2; also elsewhere on the board
+12V: C14.1, C15.1, C21.1, C22.1, C23.1, C24.1, C25.1, C26.1, C27.1, C28.1, JP24.3 (B), JP25.3 (B), JP28.3 (B), JP29.3 (B), Q5.3 (S), Q6.3 (S), R13.2, R15.2, U8.6 (Vdd), U9.6 (Vdd), U10.6 (Vdd), U11.6 (Vdd), U12.6 (Vdd), U13.6 (Vdd), U14.6 (Vdd), U15.6 (Vdd); also elsewhere on the board
CTL_A0: RN1.5 (R4.2), RN13.4 (R4.1); also elsewhere on the board
CTL_A1: RN1.6 (R3.2), RN13.3 (R3.1); also elsewhere on the board
CTL_A2: RN1.7 (R2.2), RN13.2 (R2.1); also elsewhere on the board
CTL_A3: RN1.8 (R1.2), RN13.1 (R1.1); also elsewhere on the board
CTL_A4: RN2.5 (R4.2), RN14.4 (R4.1); also elsewhere on the board
CTL_A5: RN2.6 (R3.2), RN14.3 (R3.1); also elsewhere on the board
CTL_A6: RN2.7 (R2.2), RN14.2 (R2.1); also elsewhere on the board
CTL_A7: RN2.8 (R1.2), RN14.1 (R1.1); also elsewhere on the board
CTL_B0: RN3.5 (R4.2), RN15.4 (R4.1), U8.2 (IN_A); also elsewhere on the board
CTL_B1: RN3.6 (R3.2), RN15.3 (R3.1), U8.4 (IN_B); also elsewhere on the board
CTL_B2: RN3.7 (R2.2), RN15.2 (R2.1), U9.2 (IN_A); also elsewhere on the board
CTL_B3: RN3.8 (R1.2), RN15.1 (R1.1), U9.4 (IN_B); also elsewhere on the board
CTL_B4: RN4.5 (R4.2), RN16.4 (R4.1), U10.2 (IN_A); also elsewhere on the board
CTL_B5: RN4.6 (R3.2), RN16.3 (R3.1), U10.4 (IN_B); also elsewhere on the board
CTL_B6: RN4.7 (R2.2), RN16.2 (R2.1), U11.2 (IN_A); also elsewhere on the board
CTL_B7: RN4.8 (R1.2), RN16.1 (R1.1), U11.4 (IN_B); also elsewhere on the board
CTL_C0: RN5.5 (R4.2), RN17.4 (R4.1), U12.2 (IN_A); also elsewhere on the board
CTL_C1: RN5.6 (R3.2), RN17.3 (R3.1), U12.4 (IN_B); also elsewhere on the board
CTL_C2: RN5.7 (R2.2), RN17.2 (R2.1), U13.2 (IN_A); also elsewhere on the board
CTL_C3: RN5.8 (R1.2), RN17.1 (R1.1), U13.4 (IN_B); also elsewhere on the board
CTL_C4: RN6.5 (R4.2), RN18.4 (R4.1), U14.2 (IN_A); also elsewhere on the board
CTL_C5: RN6.6 (R3.2), RN18.3 (R3.1), U14.4 (IN_B); also elsewhere on the board
CTL_C6: RN6.7 (R2.2), RN18.2 (R2.1), U15.2 (IN_A); also elsewhere on the board
CTL_C7: RN6.8 (R1.2), RN18.1 (R1.1), U15.4 (IN_B); also elsewhere on the board
GND: C21.2, C22.2, C23.2, C24.2, C25.2, C26.2, C27.2, C28.2, Q1.1 (S), Q1.4 (S), Q4.1 (S), Q4.4 (S), Q7.1 (S), Q7.4 (S), Q10.1 (S), Q10.4 (S), Q13.1 (S), Q13.4 (S), Q14.1 (S), Q14.4 (S), Q15.1 (S), Q15.4 (S), Q16.1 (S), Q16.4 (S), Q17.1 (S), Q17.4 (S), Q18.1 (S), Q18.4 (S), Q19.1 (S), Q19.4 (S), Q20.1 (S), Q20.4 (S), RN1.1 (R1.1), RN1.2 (R2.1), RN1.3 (R3.1), RN2.1 (R1.1), RN2.2 (R2.1), RN2.3 (R3.1), RN2.4 (R4.1), RN3.1 (R1.1), RN3.2 (R2.1), RN3.3 (R3.1), RN4.1 (R1.1), RN4.2 (R2.1), RN4.3 (R3.1), RN4.4 (R4.1), RN5.1 (R1.1), RN5.2 (R2.1), RN5.3 (R3.1), RN6.1 (R1.1), RN6.2 (R2.1), RN6.3 (R3.1), RN6.4 (R4.1), U8.3 (GND), U9.3 (GND), U10.3 (GND), U11.3 (GND), U12.3 (GND), U13.3 (GND), U14.3 (GND), U15.3 (GND); also elsewhere on the board
MOS_A0: Q1.5 (G), RN13.5 (R4.2)
MOS_A1: Q1.2 (G), RN13.6 (R3.2)
MOS_A2: Q4.5 (G), RN13.7 (R2.2)
MOS_A3: Q4.2 (G), RN13.8 (R1.2)
MOS_A4: Q7.5 (G), RN14.5 (R4.2)
MOS_A5: Q7.2 (G), RN14.6 (R3.2)
MOS_A6: Q10.5 (G), RN14.7 (R2.2)
MOS_A7: Q10.2 (G), RN14.8 (R1.2)
MOS_B0: Q13.2 (G), RN15.5 (R4.2)
MOS_B1: Q13.5 (G), RN15.6 (R3.2)
MOS_B2: Q14.2 (G), RN15.7 (R2.2)
MOS_B3: Q14.5 (G), RN15.8 (R1.2)
MOS_B4: Q15.2 (G), RN16.5 (R4.2)
MOS_B5: Q15.5 (G), RN16.6 (R3.2)
MOS_B6: Q16.2 (G), RN16.7 (R2.2)
MOS_B7: Q16.5 (G), RN16.8 (R1.2)
MOS_C0: Q17.2 (G), RN17.5 (R4.2)
MOS_C1: Q17.5 (G), RN17.6 (R3.2)
MOS_C2: Q18.2 (G), RN17.7 (R2.2)
MOS_C3: Q18.5 (G), RN17.8 (R1.2)
MOS_C4: Q19.2 (G), RN18.5 (R4.2)
MOS_C5: Q19.5 (G), RN18.6 (R3.2)
MOS_C6: Q20.2 (G), RN18.7 (R2.2)
MOS_C7: Q20.5 (G), RN18.8 (R1.2)
unnamed: C12.2, Q2.1 (G), R10.2
unnamed: C13.2, Q3.1 (G), R12.2
unnamed: C14.2, Q5.1 (G), R14.2
unnamed: C15.2, Q6.1 (G), R16.2
unnamed: C16.1, JP24.2 (C), Q8.3 (S), R17.2
unnamed: C16.2, Q8.1 (G), R18.2
unnamed: C17.1, JP25.2 (C), Q9.3 (S), R19.2
unnamed: C17.2, Q9.1 (G), R20.2
unnamed: C18.1, JP28.2 (C), Q11.3 (S), R21.2
unnamed: C18.2, Q11.1 (G), R22.2
unnamed: C19.1, JP29.2 (C), Q12.3 (S), R23.2
unnamed: C19.2, Q12.1 (G), R26.2
unnamed: JP14.1 (A), Q1.3 (D), R9.1, R10.1
unnamed: JP15.1 (A), Q1.6 (D), R11.1, R12.1
unnamed: JP18.1 (A), Q4.3 (D), R13.1, R14.1
unnamed: JP19.1 (A), Q4.6 (D), R15.1, R16.1
unnamed: JP22.1 (A), Q7.3 (D), R17.1, R18.1
unnamed: JP23.1 (A), Q7.6 (D), R19.1, R20.1
unnamed: JP26.1 (A), Q10.3 (D), R21.1, R22.1
unnamed: JP27.1 (A), Q10.6 (D), R23.1, R26.1
OUT_A0: JP14.2 (B), Q2.2 (D); also elsewhere on the board
OUT_A1: JP15.2 (B), Q3.2 (D); also elsewhere on the board
OUT_A2: JP18.2 (B), Q5.2 (D); also elsewhere on the board
OUT_A3: JP19.2 (B), Q6.2 (D); also elsewhere on the board
OUT_A4: JP22.2 (B), Q8.2 (D); also elsewhere on the board
OUT_A5: JP23.2 (B), Q9.2 (D); also elsewhere on the board
OUT_A6: JP26.2 (B), Q11.2 (D); also elsewhere on the board
OUT_A7: JP27.2 (B), Q12.2 (D); also elsewhere on the board
OUT_B0: Q13.6 (D), U8.7 (OUT_A); also elsewhere on the board
OUT_B1: Q13.3 (D), U8.5 (OUT_B); also elsewhere on the board
OUT_B2: Q14.6 (D), U9.7 (OUT_A); also elsewhere on the board
OUT_B3: Q14.3 (D), U9.5 (OUT_B); also elsewhere on the board
OUT_B4: Q15.6 (D), U10.7 (OUT_A); also elsewhere on the board
OUT_B5: Q15.3 (D), U10.5 (OUT_B); also elsewhere on the board
OUT_B6: Q16.6 (D), U11.7 (OUT_A); also elsewhere on the board
OUT_B7: Q16.3 (D), U11.5 (OUT_B); also elsewhere on the board
OUT_C0: Q17.6 (D), U12.7 (OUT_A); also elsewhere on the board
OUT_C1: Q17.3 (D), U12.5 (OUT_B); also elsewhere on the board
OUT_C2: Q18.6 (D), U13.7 (OUT_A); also elsewhere on the board
OUT_C3: Q18.3 (D), U13.5 (OUT_B); also elsewhere on the board
OUT_C4: Q19.6 (D), U14.7 (OUT_A); also elsewhere on the board
OUT_C5: Q19.3 (D), U14.5 (OUT_B); also elsewhere on the board
OUT_C6: Q20.6 (D), U15.7 (OUT_A); also elsewhere on the board
OUT_C7: Q20.3 (D), U15.5 (OUT_B); also elsewhere on the board

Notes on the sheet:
Yes
Jumped
Populate the P-FET, the 10K resistor, and a 1k gate resistor
For the ±1.5A range: Populate the dual MOSFET driver only
Dual Driver
+16A
P MOSFET
5V -500mA or +16A
add far too many bypass caps to each of the MOSFET drivers
For Bank A:
Ranges: -500mA +16A
12V -500mA or +16A
5V or 12V -500mA or +16A
Jump the 3 position jumper to select the voltage (if available)
Each channel or pair has several configurable output modes.
For the -500mA range: Populate the dual MOSFET only
Open
Mode
Only channel A can do the +16A with optional soft start range.
Bank A
+16A W/ Soft Start
Do not populate any component not specified in the table
Dual MOSFET
IO Pulldowns
Only channels B and C can do the ±1.5A range
Gate Resistors
Channel Configuration Instructions:
To add soft start: Use a 680k gate resistor and populate the capacitor
All channels can do the -500mA range.
2pad Jumper
Bank B
Ranges: -500mA ±1.5A
CHx0 will turn on during boot
See design notes on how to populate this area of the circuit to configre output behavior
For the -500mA range: Jump the 2 position jumper for that channel
680k
Both channels in the pair mmust be configured identically
For the +16A range:
Rgate
Never populate the dual MOSFET and the MOSFET driver on the same channel pair

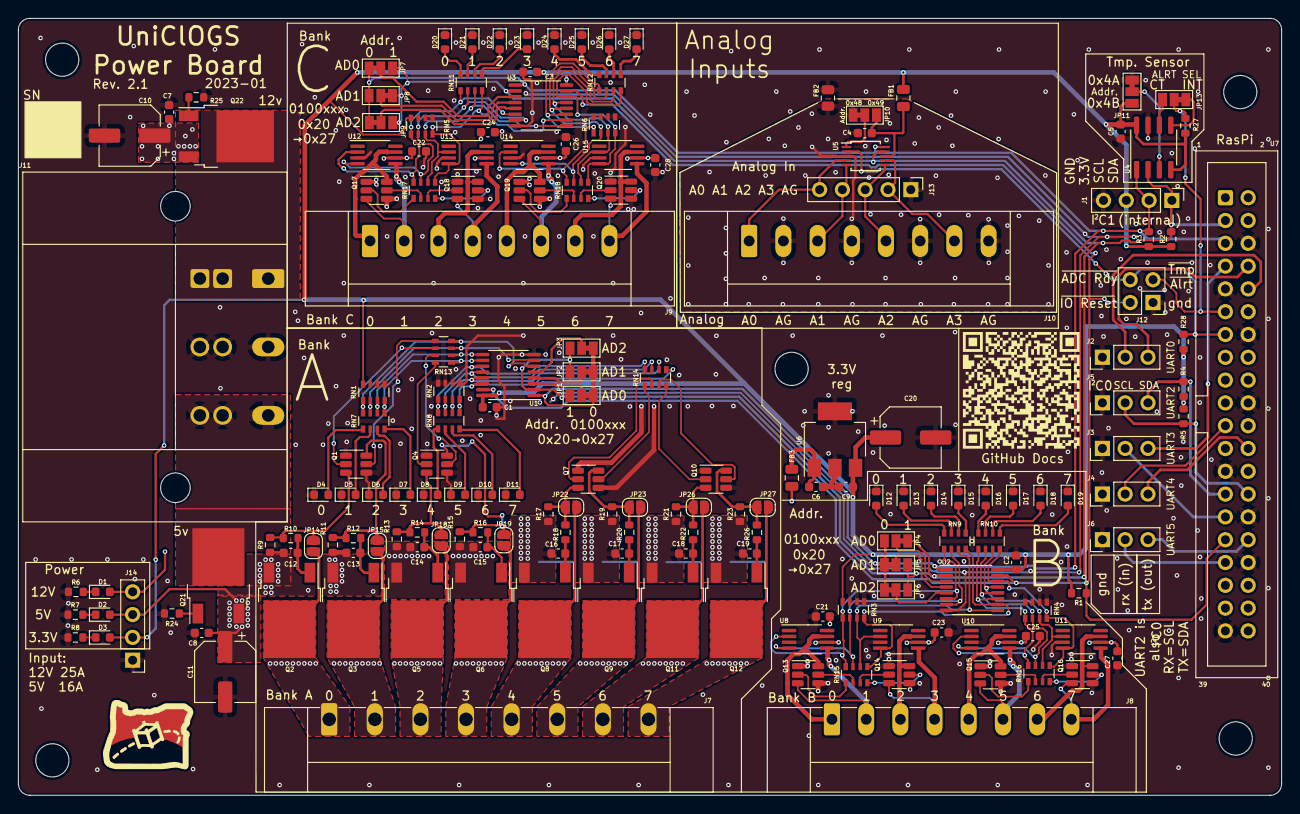
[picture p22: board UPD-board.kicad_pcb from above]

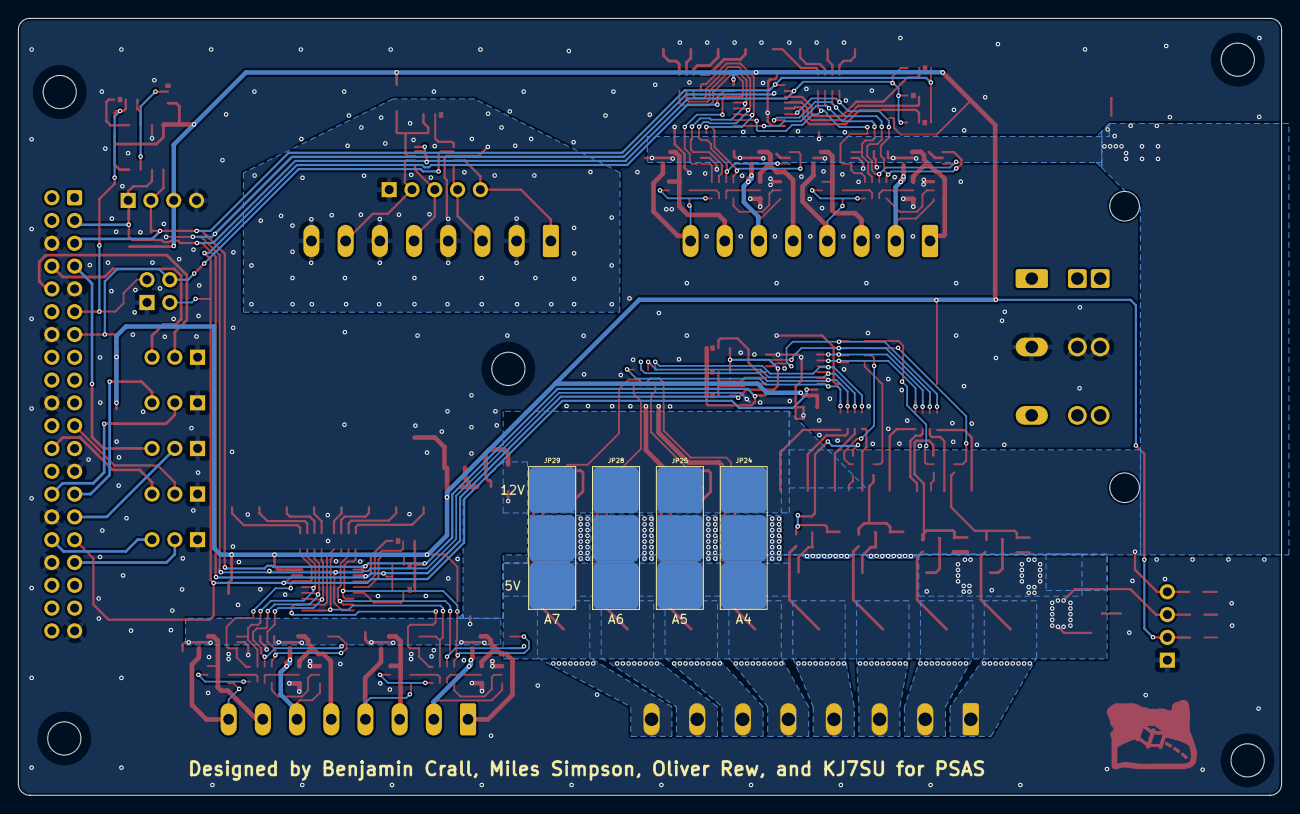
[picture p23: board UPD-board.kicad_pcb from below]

Board: 2 copper layers, 140.7 x 86.5 mm, 185 parts (4 on the bottom side), 162 nets.

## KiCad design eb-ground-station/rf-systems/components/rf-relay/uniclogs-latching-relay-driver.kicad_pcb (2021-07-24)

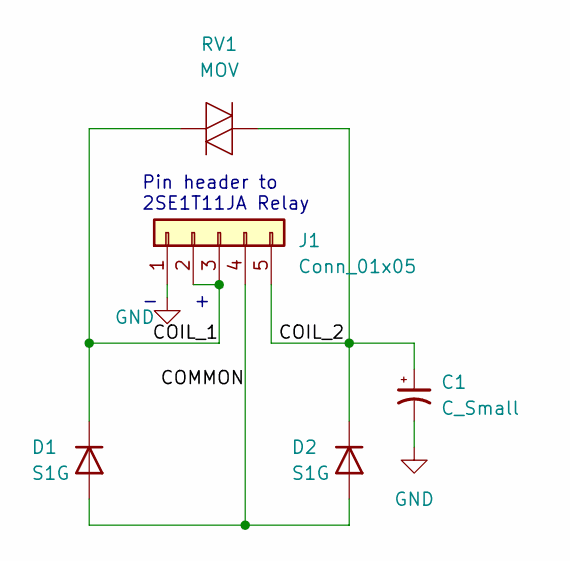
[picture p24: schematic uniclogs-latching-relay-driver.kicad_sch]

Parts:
C1: C_Small; CP_Elec_16x16.8
D1, D2: S1G; D_SMA
J1: Conn_01x05; 2-3_1x05_2.54mm
RV1: MOV; 2220_MOV

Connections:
/COIL_1: D1.1 (K), J1.2, J1.3, RV1.1
/COIL_2: C1.1, D2.1 (K), J1.5, RV1.2
/COMMON: D1.2 (A), D2.2 (A), J1.4
GND: C1.2, J1.1

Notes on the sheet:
Pin header to 2SE1T11JA Relay

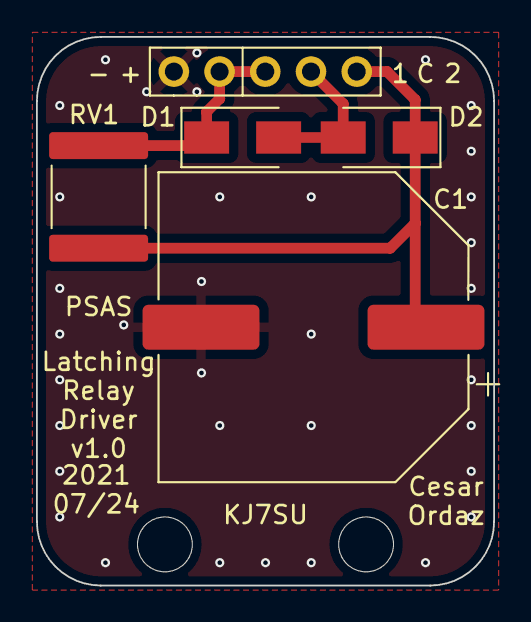
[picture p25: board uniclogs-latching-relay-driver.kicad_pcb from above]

Board: 2 copper layers, 25.4 x 30.5 mm, 5 parts (0 on the bottom side), 4 nets.

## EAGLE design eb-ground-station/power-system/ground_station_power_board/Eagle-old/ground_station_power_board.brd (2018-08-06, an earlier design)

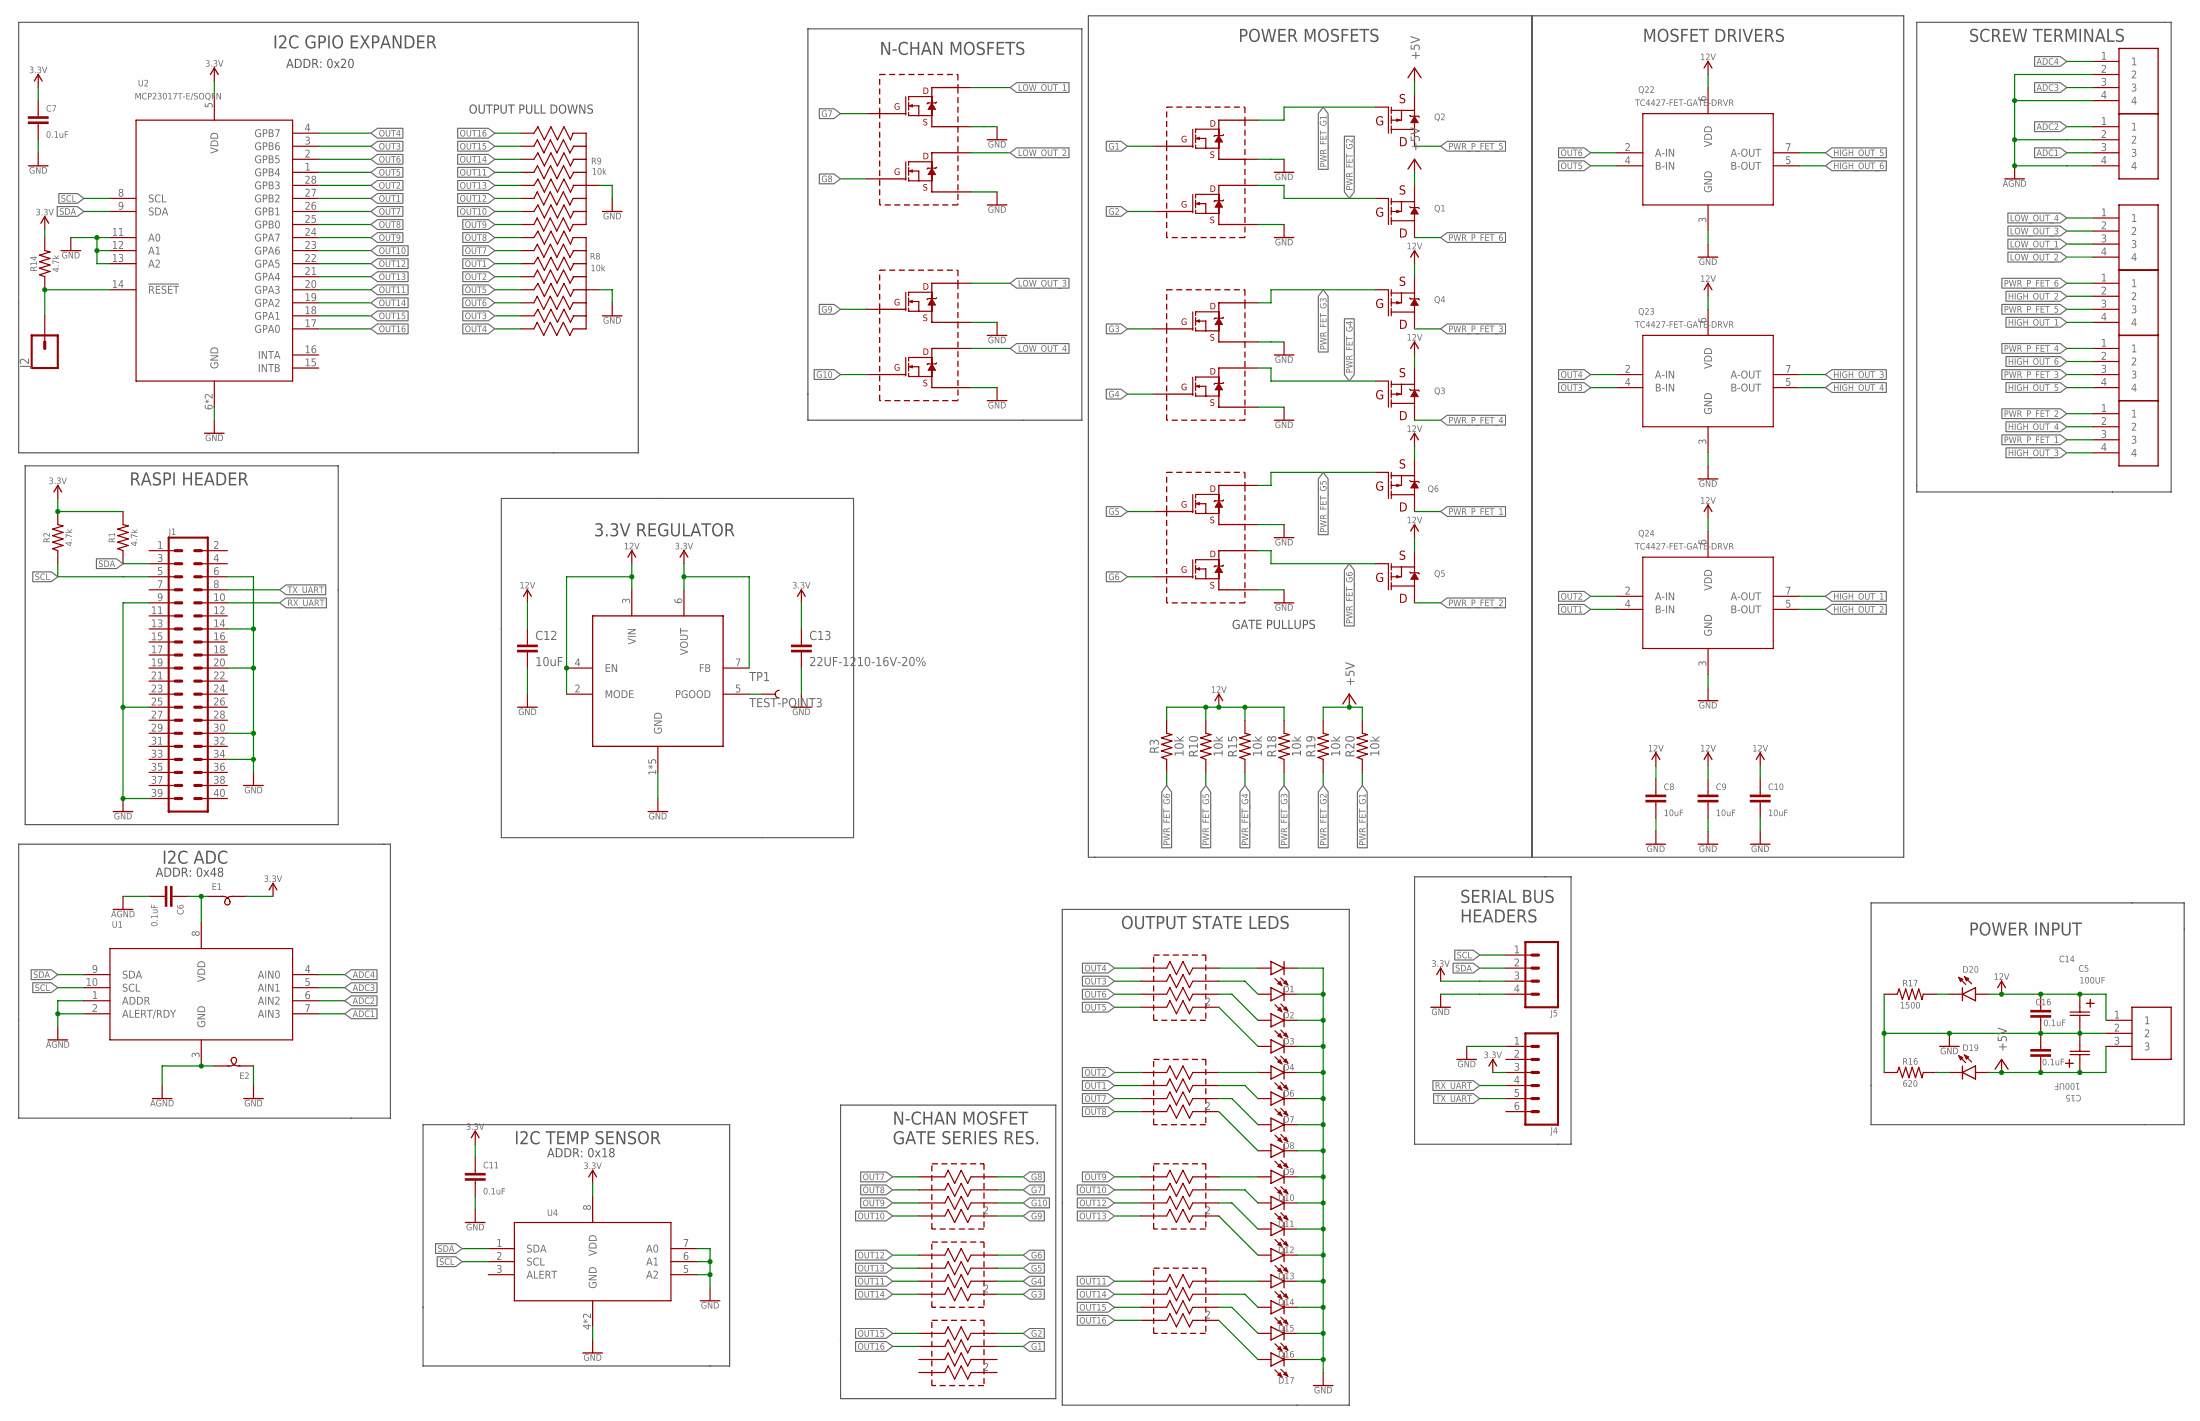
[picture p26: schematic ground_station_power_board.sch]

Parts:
C5, C15: 100UF; CHEMI-KE0-M
C6, C7, C11, C14, C16: 0.1uF; 0603
C8, C9, C10: 10uF; 0805
C12: 10uF; 1206
C13: 22UF-1210-16V-20%; 1210
D1, D2, D3, D4, D6, D7, D8, D9, D10, D11, D12, D13, D14, D15, D16, D17, D19, D20: LED0603; LED-0603
E1, E2: L-BEAD-0805-B; .0805-B
J1: CONN_20X2SHROUDED; 2X20_SHROUDED
J2: CONN_01PTH_NO_SILK_KIT; 1X01NS_KIT
J4: CONN_06LONGPADS; 1X06_LONGPADS
J5: CONN_04LONGPADS; 1X04_LONGPADS
Q1, Q2, Q3, Q4, Q5, Q6: SQJ459EP_MOSFET_P_CHAN; POWERPAK_S0-8L
Q8, Q9, Q15, Q17, Q18: DMN61D8LVT-DUAL-N-CHANNEL-MOSFET; TSOT26
Q22, Q23, Q24: TC4427-FET-GATE-DRVR; TSSOP-8
R1, R2, R14: 4.7k; 0603
R3, R10, R15, R18, R19, R20: 10k; 0603
R4, R5, R6, R7: 680; RES-ARRAY-742C083
R8, R9: 10k; C_ARRAY_EXBA-M
R11, R12, R13: 220; RES-ARRAY-742C083
R16: 620; 0603
R17: 1500; 0603
TP1: TEST-POINT3; PAD.03X.03
U1: ADS1115IDGSTDGS10-M; DGS10-M
U2: MCP23017T-E/SOQFN; QFN28_6X6MC-M
U4: MCP9808T-E/MCDFN8_2X3MC-M; DFN8_2X3MC-M
U$1, U$2, U$3, U$4, U$5, U$6: 1719031-PHONEIX-CONTACT-DBL-TERMINAL-BLOCK
U$9: LMZM23601V3SILT; MICRO-SIP
U$11: 1714968-PHONEIX-CONTACT-TERMINAL-BLOCK; 1714968-PHONEIX-CONTACT-3-TERMINAL-BLOCK

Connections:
3.3V: C7.1, C11.1, C13.1, E1.2, J4.3, J5.3, R1.2, R2.2, R14.2, U2.5 (VDD), U4.8 (VDD), U$9.6 (VOUT), U$9.7 (FB)
12V: C5.1 (11), C8.1, C9.1, C10.1, C12.1, C14.1, D20.A, Q3.S1 (S), Q3.S2 (S), Q3.S3 (S), Q4.S1 (S), Q4.S2 (S), Q4.S3 (S), Q5.S1 (S), Q5.S2 (S), Q5.S3 (S), Q6.S1 (S), Q6.S2 (S), Q6.S3 (S), Q22.6 (VDD), Q23.6 (VDD), Q24.6 (VDD), R3.2, R10.2, R15.2, R18.2, U$9.2 (MODE), U$9.3 (VIN), U$9.4 (EN), U$11.1
+5V: C15.1 (11), C16.2, D19.A, Q1.S1 (S), Q1.S2 (S), Q1.S3 (S), Q2.S1 (S), Q2.S2 (S), Q2.S3 (S), R19.2, R20.2, U$11.3
ADC1: U1.7 (AIN3), U$5.3
ADC2: U1.6 (AIN2), U$5.1
ADC3: U1.5 (AIN1), U$6.3
ADC4: U1.4 (AIN0), U$6.1
AGND: C6.2, E2.2, U1.1 (ADDR), U1.2 (ALERT/RDY), U1.3 (GND), U$5.2, U$5.4, U$6.2, U$6.4
G1: Q8.5 (G2), R11.6 (!1OE6)
G2: Q8.2 (G1), R11.8 (!1OE8)
G3: Q9.5 (G2), R12.2 (!1OE2)
G4: Q9.2 (G1), R12.4 (!1OE4)
G5: Q15.5 (G2), R12.6 (!1OE6)
G6: Q15.2 (G1), R12.8 (!1OE8)
G7: Q18.5 (G2), R13.6 (!1OE6)
G8: Q18.2 (G1), R13.8 (!1OE8)
G9: Q17.5 (G2), R13.2 (!1OE2)
G10: Q17.2 (G1), R13.4 (!1OE4)
GND: C5.2 (22), C7.2, C8.2, C9.2, C10.2, C11.2, C12.2, C13.2, C14.2, C15.2 (22), C16.1, D1.C, D2.C, D3.C, D4.C, D6.C, D7.C, D8.C, D9.C, D10.C, D11.C, D12.C, D13.C, D14.C, D15.C, D16.C, D17.C, E2.1, J1.6, J1.9, J1.14, J1.20, J1.25, J1.30, J1.34, J1.39, J4.1, J5.4, Q8.1 (S1), Q8.4 (S2), Q9.1 (S1), Q9.4 (S2), Q15.1 (S1), Q15.4 (S2), Q17.1 (S1), Q17.4 (S2), Q18.1 (S1), Q18.4 (S2), Q22.3 (GND), Q23.3 (GND), Q24.3 (GND), R8.5 (55), R8.10 (55), R9.5 (55), R9.10 (55), R16.1, R17.1, U2.6 (GND), U2.11 (A0), U2.12 (A1), U2.13 (A2), U2.29 (GND), U4.4 (GND), U4.5 (A2), U4.6 (A1), U4.7 (A0), U4.9 (GND), U$9.1 (GND), U$9.TP (GND), U$9.V1 (GND), U$9.V2 (GND), U$9.V3 (GND), U$11.2
HIGH_OUT_1: Q24.7 (A-OUT), U$3.4
HIGH_OUT_2: Q24.5 (B-OUT), U$3.2
HIGH_OUT_3: Q23.7 (A-OUT), U$1.4
HIGH_OUT_4: Q23.5 (B-OUT), U$1.2
HIGH_OUT_5: Q22.7 (A-OUT), U$2.4
HIGH_OUT_6: Q22.5 (B-OUT), U$2.2
LOW_OUT_1: Q18.3 (D2), U$4.3
LOW_OUT_2: Q18.6 (D1), U$4.4
LOW_OUT_3: Q17.3 (D2), U$4.2
LOW_OUT_4: Q17.6 (D1), U$4.1
unnamed: D1.A, R4.8 (!1OE8)
unnamed: D2.A, R4.6 (!1OE6)
unnamed: D3.A, R4.4 (!1OE4)
unnamed: D4.A, R4.2 (!1OE2)
unnamed: C6.1, E1.1, U1.8 (VDD)
unnamed: J2.1, R14.1, U2.14 (!RESET)
unnamed: TP1.P$1, U$9.5 (PGOOD)
unnamed: D19.C, R16.2
unnamed: D6.A, R5.8 (!1OE8)
unnamed: D7.A, R5.6 (!1OE6)
unnamed: D8.A, R5.4 (!1OE4)
unnamed: D9.A, R5.2 (!1OE2)
unnamed: D20.C, R17.2
unnamed: D10.A, R6.8 (!1OE8)
unnamed: D11.A, R6.6 (!1OE6)
unnamed: D12.A, R6.4 (!1OE4)
unnamed: D13.A, R6.2 (!1OE2)
unnamed: D14.A, R7.8 (!1OE8)
unnamed: D15.A, R7.6 (!1OE6)
unnamed: D16.A, R7.4 (!1OE4)
unnamed: D17.A, R7.2 (!1OE2)
OUT1: Q24.4 (B-IN), R5.5 (!1OE5), R8.2 (22), U2.27 (GPB2)
OUT2: Q24.2 (A-IN), R5.7 (!1OE7), R8.8 (88), U2.28 (GPB3)
OUT3: Q23.4 (B-IN), R4.5 (!1OE5), R8.4 (44), U2.3 (GPB6)
OUT4: Q23.2 (A-IN), R4.7 (!1OE7), R8.6 (66), U2.4 (GPB7)
OUT5: Q22.4 (B-IN), R4.1 (!1OE1), R8.3 (33), U2.1 (GPB4)
OUT6: Q22.2 (A-IN), R4.3 (!1OE3), R8.7 (77), U2.2 (GPB5)
OUT7: R5.3 (!1OE3), R8.9 (99), R13.7 (!1OE7), U2.26 (GPB1)
OUT8: R5.1 (!1OE1), R8.1 (11), R13.5 (!1OE5), U2.25 (GPB0)
OUT9: R6.7 (!1OE7), R9.6 (66), R13.3 (!1OE3), U2.24 (GPA7)
OUT10: R6.5 (!1OE5), R9.4 (44), R13.1 (!1OE1), U2.23 (GPA6)
OUT11: R7.7 (!1OE7), R9.8 (88), R12.3 (!1OE3), U2.20 (GPA3)
OUT12: R6.3 (!1OE3), R9.7 (77), R12.7 (!1OE7), U2.22 (GPA5)
OUT13: R6.1 (!1OE1), R9.3 (33), R12.5 (!1OE5), U2.21 (GPA4)
OUT14: R7.5 (!1OE5), R9.2 (22), R12.1 (!1OE1), U2.19 (GPA2)
OUT15: R7.3 (!1OE3), R9.9 (99), R11.7 (!1OE7), U2.18 (GPA1)
OUT16: R7.1 (!1OE1), R9.1 (11), R11.5 (!1OE5), U2.17 (GPA0)
PWR_FET_G1: Q2.G, Q8.3 (D2), R20.1
PWR_FET_G2: Q1.G, Q8.6 (D1), R19.1
PWR_FET_G3: Q4.G, Q9.3 (D2), R18.1
PWR_FET_G4: Q3.G, Q9.6 (D1), R15.1
PWR_FET_G5: Q6.G, Q15.3 (D2), R10.1
PWR_FET_G6: Q5.G, Q15.6 (D1), R3.1
PWR_P_FET_1: Q6.D1 (D), U$1.3
PWR_P_FET_2: Q5.D1 (D), U$1.1
PWR_P_FET_3: Q4.D1 (D), U$2.3
PWR_P_FET_4: Q3.D1 (D), U$2.1
PWR_P_FET_5: Q2.D1 (D), U$3.3
PWR_P_FET_6: Q1.D1 (D), U$3.1
RX_UART: J1.10, J4.4
SCL: J1.5, J5.1, R2.1, U1.10 (SCL), U2.8 (SCL), U4.2 (SCL)
SDA: J1.3, J5.2, R1.1, U1.9 (SDA), U2.9 (SDA), U4.1 (SDA)
TX_UART: J1.8, J4.5

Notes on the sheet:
SCREW TERMINALS
MOSFET DRIVERS
N-CHAN MOSFET GATE SERIES RES.
POWER MOSFETS
N-CHAN MOSFETS
GATE PULLUPS
OUTPUT PULL DOWNS
SERIAL BUS HEADERS
I2C GPIO EXPANDER
OUTPUT STATE LEDS
RASPI HEADER
I2C TEMP SENSOR
I2C ADC
ADDR: 0x20
ADDR: 0x48
ADDR: 0x18
3.3V REGULATOR
POWER INPUT

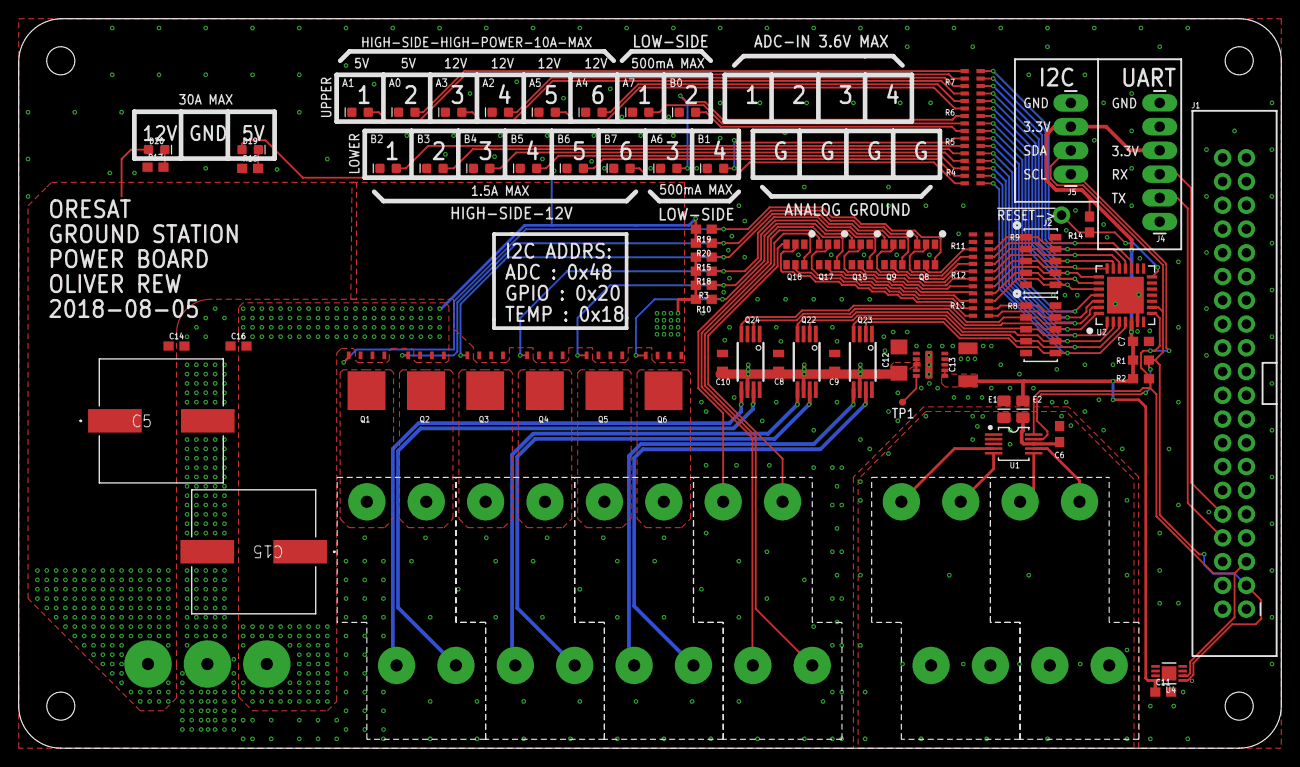
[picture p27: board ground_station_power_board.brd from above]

Board: 2 copper layers, 135.0 x 78.0 mm, 83 parts (1 on the bottom side), 82 nets.

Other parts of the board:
U$8: PSAS_LOGO_15X15

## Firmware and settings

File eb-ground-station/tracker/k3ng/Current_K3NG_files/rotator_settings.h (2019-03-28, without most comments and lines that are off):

#define AZIMUTH_STARTING_POINT_DEFAULT 0 // 180      // the starting point in degrees of the azimuthal rotator - only used for initializing EEPROM the first time the code is run
#define AZIMUTH_ROTATION_CAPABILITY_DEFAULT 450 // the default rotation capability of the rotator in degrees - only used for initializing EEPROM the first time the code is run
#define ELEVATION_MAXIMUM_DEGREES 180           // change this to set the maximum elevation in degrees
#define ANALOG_AZ_FULL_CCW 4
#define ANALOG_AZ_FULL_CW 1009
#define ANALOG_EL_0_DEGREES 2
#define ANALOG_EL_MAX_ELEVATION 1018  // maximum elevation is normally 180 degrees unless change below for ELEVATION_MAXIMUM_DEGREES
#define ANALOG_AZ_OVERLAP_DEGREES 540         // if overlap_led above is enabled, turn on overlap led line if azimuth is greater than this setting
#define OPTION_OVERLAP_LED_BLINK_MS 100
#define PWM_SPEED_VOLTAGE_X1  64         // 0 to 255
#define PWM_SPEED_VOLTAGE_X2  128        // 0 to 255
#define PWM_SPEED_VOLTAGE_X3  191        // 0 to 255
#define PWM_SPEED_VOLTAGE_X4  253        // 0 to 255
#define AZ_SLOWSTART_DEFAULT 0            // 0 = off ; 1 = on
#define AZ_SLOWDOWN_DEFAULT 0             // 0 = off ; 1 = on
#define AZ_SLOW_START_UP_TIME 2000        // if slow start is enabled, the unit will ramp up speed for this many milliseconds
#define AZ_SLOW_START_STARTING_PWM 1      // PWM starting value for slow start (must be < 256)
#define AZ_SLOW_START_STEPS 20            // must be < 256
#define SLOW_DOWN_BEFORE_TARGET_AZ 10.0  // if slow down is enabled, slowdown will be activated within this many degrees of target azimuth
#define AZ_SLOW_DOWN_PWM_START 200         // starting PWM value for slow down (must be < 256)
#define	AZ_SLOW_DOWN_PWM_STOP 20          // ending PWM value for slow down (must be < 256)
#define AZ_SLOW_DOWN_STEPS 200 //20       // must be < 256
#define AZ_INITIALLY_IN_SLOW_DOWN_PWM 50  // PWM value to start at if we're starting in the slow down zone (1 - 255)
#define EL_SLOWSTART_DEFAULT 0            // 0 = off ; 1 = on
#define EL_SLOWDOWN_DEFAULT 0             // 0 = off ; 1 = on
#define EL_SLOW_START_UP_TIME 2000        // if slow start is enabled, the unit will ramp up speed for this many milliseconds
#define EL_SLOW_START_STARTING_PWM 1      // PWM starting value for slow start  (must be < 256)
#define EL_SLOW_START_STEPS 20            // must be < 256
#define SLOW_DOWN_BEFORE_TARGET_EL 10.0  // if slow down is enabled, slowdown will be activated within this many degrees of target elevation
#define EL_SLOW_DOWN_PWM_START 200         // starting PWM value for slow down (must be < 256)
#define	EL_SLOW_DOWN_PWM_STOP 20          // ending PWM value for slow down (must be < 256)
#define EL_SLOW_DOWN_STEPS 20
#define EL_INITIALLY_IN_SLOW_DOWN_PWM 50  // PWM value to start at if we're starting in the slow down zone (1 - 255)
#define TIMED_SLOW_DOWN_TIME 2000
#define AZ_VARIABLE_FREQ_OUTPUT_LOW   31     // Frequency in hertz of minimum speed
#define AZ_VARIABLE_FREQ_OUTPUT_HIGH 5000 //100    // Frequency in hertz of maximum speed
#define EL_VARIABLE_FREQ_OUTPUT_LOW   31     // Frequency in hertz of minimum speed
#define EL_VARIABLE_FREQ_OUTPUT_HIGH 100    // Frequency in hertz of maximum speed
#define AZ_MANUAL_ROTATE_CCW_LIMIT 0   // if using a rotator that starts at 180 degrees, set this to something like 185
#define AZ_MANUAL_ROTATE_CW_LIMIT 535  // add 360 to this if you go past 0 degrees (i.e. 180 CW after 0 degrees = 540)
#define EL_MANUAL_ROTATE_DOWN_LIMIT -1
#define EL_MANUAL_ROTATE_UP_LIMIT 181
#define SPEED_POT_LOW 0
#define SPEED_POT_HIGH 1023
#define SPEED_POT_LOW_MAP 1
#define SPEED_POT_HIGH_MAP 255
#define AZ_PRESET_POT_FULL_CW 0
#define AZ_PRESET_POT_FULL_CCW 1023
#define AZ_PRESET_POT_FULL_CW_MAP 180         // azimuth pot fully counter-clockwise degrees
#define AZ_PRESET_POT_FULL_CCW_MAP 630        // azimuth pot fully clockwise degrees
#define ENCODER_PRESET_TIMEOUT 5000
#define AZIMUTH_TOLERANCE 3.0            // rotator will stop within X degrees when doing autorotation
#define ELEVATION_TOLERANCE 0.1 //1.0
#define OPERATION_TIMEOUT 120000        // timeout for any rotation operation in mS ; 120 seconds is usually enough unless you have the speed turned down
#define TIMED_INTERVAL_ARRAY_SIZE 20
#define CONTROL_PORT_BAUD_RATE 9600
#define REMOTE_UNIT_PORT_BAUD_RATE 9600
#define GPS_PORT_BAUD_RATE 9600
#define GPS_MIRROR_PORT_BAUD_RATE 9600
#define CONTROL_PORT_MAPPED_TO &Serial  // change this line to map the control port to a different serial port (Serial1, Serial2, etc.)
#define GPS_PORT_MAPPED_TO &Serial2  // change this line to map the GPS port to a different serial port
#define OPTION_SEND_STRING_OUT_CONTROL_PORT_WHEN_INITIALIZING_STRING ("test\n\r")
#define LCD_COLUMNS 20 //16
#define LCD_ROWS 4 //2       // this is automatically set below for HARDWARE_EA4TX_ARS_USB and HARDWARE_M0UPU
#define LCD_UPDATE_TIME 1000           // LCD update time in milliseconds
#define LCD_HHMM_CLOCK_POSITION LEFT          //LEFT or RIGHT
#define LCD_HHMMSS_CLOCK_POSITION LEFT          //LEFT or RIGHT
#define LCD_ALT_HHMM_CLOCK_AND_MAIDENHEAD_POSITION LEFT
#define LCD_ALT_HHMM_CLOCK_AND_MAIDENHEAD_ROW 1
#define LCD_CONSTANT_HHMMSS_CLOCK_AND_MAIDENHEAD_POSITION CENTER
#define LCD_CONSTANT_HHMMSS_CLOCK_AND_MAIDENHEAD_ROW 3
#define LCD_BIG_CLOCK_ROW 4
#define LCD_GPS_INDICATOR_POSITION RIGHT //LEFT or RIGHT
#define LCD_GPS_INDICATOR_ROW 1
#define LCD_MOON_TRACKING_ROW 3                                   // LCD display row for OPTION_DISPLAY_MOON_TRACKING_CONTINUOUSLY
#define LCD_MOON_TRACKING_UPDATE_INTERVAL 5000
#define LCD_SUN_TRACKING_ROW 4                                    // LCD display row for OPTION_DISPLAY_SUN_TRACKING_CONTINUOUSLY
#define LCD_SUN_TRACKING_UPDATE_INTERVAL 5000
#define LCD_MOON_OR_SUN_TRACKING_CONDITIONAL_ROW 3                // LCD display row for OPTION_DISPLAY_MOON_OR_SUN_TRACKING_CONDITIONAL
#define SPLASH_SCREEN_TIME 3000
#define LCD_HEADING_ROW 2
#define LCD_HEADING_FIELD_SIZE 20
#define LCD_AZ_ONLY_HEADING_ROW 1
#define LCD_AZ_ONLY_HEADING_FIELD_SIZE 20
#define LCD_EL_ONLY_HEADING_ROW 2
#define LCD_EL_ONLY_HEADING_FIELD_SIZE 20
#define LCD_STATUS_ROW 1
#define LCD_STATUS_FIELD_SIZE 20
#define LCD_DIRECTION_ROW 1
#define LCD_HHMMSS_CLOCK_ROW 1
#define LCD_HHMM_CLOCK_ROW 1
#define PARKING_STATUS_DISPLAY_TIME_MS 5000
#define AZ_BRAKE_DELAY 3000            // in milliseconds
#define EL_BRAKE_DELAY 3000            // in milliseconds
#define BRAKE_ACTIVE_STATE HIGH
#define BRAKE_INACTIVE_STATE LOW
#define EEPROM_MAGIC_NUMBER 105 // 109
#define EEPROM_WRITE_DIRTY_CONFIG_TIME  30  //time in seconds
#if defined(FEATURE_TWO_DECIMAL_PLACE_HEADINGS)
#define HEADING_MULTIPLIER 100L
#define LCD_HEADING_MULTIPLIER 100.0
#define LCD_DECIMAL_PLACES 2
#endif //FEATURE_TWO_DECIMAL_PLACE_HEADINGS
#if defined(FEATURE_ONE_DECIMAL_PLACE_HEADINGS)
#define HEADING_MULTIPLIER 10
#define LCD_HEADING_MULTIPLIER 10.0
#define LCD_DECIMAL_PLACES 1
#endif //FEATURE_ONE_DECIMAL_PLACE_HEADINGS
#if !defined(FEATURE_ONE_DECIMAL_PLACE_HEADINGS) && !defined(FEATURE_TWO_DECIMAL_PLACE_HEADINGS)
#define HEADING_MULTIPLIER 1
#define LCD_HEADING_MULTIPLIER 1.0
#define LCD_DECIMAL_PLACES 0
#endif //!defined(FEATURE_ONE_DECIMAL_PLACE_HEADINGS) && !defined(FEATURE_TWO_DECIMAL_PLACE_HEADINGS)
#define AZ_POSITION_ROTARY_ENCODER_DEG_PER_PULSE 0.5
#define EL_POSITION_ROTARY_ENCODER_DEG_PER_PULSE 0.5
#define AZ_POSITION_PULSE_DEG_PER_PULSE 0.5
#define EL_POSITION_PULSE_DEG_PER_PULSE 0.5
#define PARK_AZIMUTH 360.0 * HEADING_MULTIPLIER      // replace the 0.0 with your park azimuth; azimuth is in raw degrees (i.e. on a 180 degree starting point rotator, 0 degrees = 360)
#define PARK_ELEVATION 0.0 * HEADING_MULTIPLIER    // replace the 0.0 with your park elevation
#define COMMAND_BUFFER_SIZE 50
#define REMOTE_BUFFER_TIMEOUT_MS 250
#define REMOTE_UNIT_COMMAND_TIMEOUT_MS 2000
#define AZ_REMOTE_UNIT_QUERY_TIME_MS 150         // how often we query the remote remote for azimuth
#define EL_REMOTE_UNIT_QUERY_TIME_MS 150         // how often we query the remote remote for elevation
#define ROTATE_PIN_INACTIVE_VALUE LOW
#define ROTATE_PIN_ACTIVE_VALUE HIGH
#define AZIMUTH_SMOOTHING_FACTOR 0      // value = 0 to 99.9
#define ELEVATION_SMOOTHING_FACTOR 0    // value = 0 to 99.9
#define AZIMUTH_MEASUREMENT_FREQUENCY_MS 100        // this does not apply if using FEATURE_AZ_POSITION_GET_FROM_REMOTE_UNIT
#define ELEVATION_MEASUREMENT_FREQUENCY_MS 100      // this does not apply if using FEATURE_EL_POSITION_GET_FROM_REMOTE_UNIT
#define JOYSTICK_WAIT_TIME_MS 100
#define ROTATION_INDICATOR_PIN_ACTIVE_STATE HIGH
#define ROTATION_INDICATOR_PIN_INACTIVE_STATE LOW
#define ROTATION_INDICATOR_PIN_TIME_DELAY_SECONDS 0
#define ROTATION_INDICATOR_PIN_TIME_DELAY_MINUTES 0
#define AZ_POSITION_INCREMENTAL_ENCODER_PULSES_PER_REV 2000.0
#define EL_POSITION_INCREMENTAL_ENCODER_PULSES_PER_REV 2000.0
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

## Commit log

2017-08-10 Update README.md
    Put in content that explains the various parts of the primary ground station.
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2017-08-11 Delete eb-ground-station
    Woops I made a mistake!
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2017-08-18 I did a first order approximation of the rooftop ground station in solidworks using Glenn's wind loading numbers.
    [First_order_Approximate_mast_loading.SLDPRT]
2017-08-18 organized my mess
    [First_order_Approximate_mast_loading.SLDPRT]
2017-09-05 Added Mark M's photos of testing SatNOGS helix antenna in satnogs directory
2017-09-07 added organization & resources to the notebook
    [NOAA_NCDC_DAILY_FSOD_AWND_averageDailyWindSpeedData_gridtable.tsv]
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2017-09-14 Reorganized directory making subsystem directories, and pulled some of the larger issues into the README for that subsystem
    [First_order_Approximate_mast_loading.SLDPRT, NOAA_NCDC_DAILY_FSOD_AWND_averageDailyWindSpeedData_gridtable.tsv]
2017-09-14 Reorganized for independent structure, and augmented weather station. Also included component cut-sheets, and TIA documents
    [First_order_Approximate_mast_loading.SLDPRT, NOAA_NCDC_DAILY_FSOD_AWND_averageDailyWindSpeedData_gridtable.tsv]
2017-09-21 shear and bending on the ground station mast
    TODO:
    * comment the code, so I will know what it does a week from now.
    * I suppose I'm also neglecting the fact that the legs have a reaction
    in the -Z direction, which compresses the mast. That's definitely not
    negligible. I should account for that.
    * change the structure of the notebook to be intro -> tipping -> bending
    as opposed to intro -> calculation -> results
    * It seems like the bending ought to go to zero a the tip of the mast.
    Why doesn't it?
    TL;DR for the bending:
    * assume there is only 1 set of legs
    * get the reaction forces from the legs
    * form a sympy expression for load-per-length
    * integrate to get shear and bending
    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
2018-01-28 Added controller files
    [satnogs_controller.csv, satnogs_controller.sch]
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2018-07-23 Started the ground station power board
    [ground_station_power_board.sch]
2018-07-26 progress on the power board
    [ground_station_power_board.brd, ground_station_power_board.sch]
2018-07-28 Power board is mostly wrapped up
    [ground_station_power_board.brd, ground_station_power_board.sch]
2018-07-31 some final changes
    [ground_station_power_board.brd, ground_station_power_board.sch]
2018-07-31 prettied up the schematic
    [ground_station_power_board.sch]
2018-07-31 Approved ERC and DRC
    [ground_station_power_board.brd, ground_station_power_board.sch]
2018-07-31 added vias
    [ground_station_power_board.brd]
2018-07-31 I can't stop making changes HELP!
    [ground_station_power_board.brd]
2018-08-01 every time I look at this I add 40 more vias
    [ground_station_power_board.brd, ground_station_power_board.sch]
2018-08-03 added decoupling cap and some labels
    [ground_station_power_board.brd, ground_station_power_board.sch]
2018-08-03 added SMPS
    [ground_station_power_board.brd, ground_station_power_board.sch]
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2018-08-06 Updated for 2 5V mosfets
    [ground_station_power_board.brd, ground_station_power_board.sch]
2018-08-06 small fixes
    [ground_station_power_board.brd, ground_station_power_board.sch]
2018-08-06 moved some silk
    [ground_station_power_board.brd]
2018-08-06 moved via
    [ground_station_power_board.brd]
2018-08-06 label change
    [ground_station_power_board.brd]
2018-08-06 fixed logo
    [ground_station_power_board.brd]
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2018-09-17 Update Station_Board.txt
    Swapped IO points between rotator power and S-Band power.
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2019-03-28 Wiring diagrams added
    [satnogs_controller.csv, satnogs_controller.sch]
2019-04-01 Added PA test info, and moved things around
    [DEMI PA Power Test.xlsx, ground_station_power_board.brd, ground_station_power_board.sch]
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2021-07-24 Added latching relay driver board kicad files.
    [uniclogs-latching-relay-driver.kicad_pcb, uniclogs-latching-relay-driver.kicad_sch]
2021-07-24 Added BOM for latching relay driver board.
    [uniclogs-latching-relay-driver-BOM.xlsx]
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2021-09-16 Updated BOM and added design notes txt file
    [uniclogs-latching-relay-driver-BOM.xlsx]
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2022-08-24 Starting V2 in KiCad
    [UPD-board.kicad_pcb, UPD-board.kicad_sch, power_seitching.kicad_sch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]
2022-08-24 New power board schematic almost done
    [UPD-board.kicad_sch, power_switching.kicad_sch, softstart-test.kicad_sch]
2022-08-26 First layout done. No slikscreen work yet
    [UPD-board.kicad_pcb, UPD-board.kicad_sch, power_switching.kicad_sch]
2022-08-26 Added PDF schematic
    [UPD-board.kicad_pcb, UPD-board.kicad_sch, power_seitching.kicad_sch]
2022-08-27 Added soft start and ground vias
    [UPD-board.kicad_pcb, UPD-board.kicad_sch]
2022-08-27 Fixed some silkscreen
    [UPD-board.kicad_pcb]
2022-08-27 refdes silkscreen nearly done
    [UPD-board.kicad_pcb, UPD-board.kicad_sch]
2022-08-28 More silkscreen work
    [UPD-board.kicad_pcb, UPD-board.kicad_sch]
2022-08-28 Added PDFs and PNGs of the board
    [UPD-board.kicad_pcb]
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2022-08-29 Fixed ~IO_RESET RasPi pin and improved silkscreen
    [UPD-board.kicad_pcb, UPD-board.kicad_sch]
2022-08-29 Fixed some issues and added propper power input connector
    [UPD-board.kicad_pcb, UPD-board.kicad_sch]
2022-08-30 Upgrading Bank A to 16A
    [UPD-board.kicad_pcb, UPD-board.kicad_sch, power_switching.kicad_sch]
2022-09-03 Finished routing with higher current traces
    [UPD-board.kicad_pcb]
2022-09-04 Silkscreen almost done
    [UPD-board.kicad_pcb, UPD-board.kicad_sch, power_switching.kicad_sch]
2022-09-04 Made new drawings and renders
    [UPD-board.kicad_pcb, UPD-board.kicad_sch]
2022-09-05 Fixed issues discovered during the design review
    [UPD-board.kicad_pcb, UPD-board.kicad_sch, power_switching.kicad_sch]
2022-09-06 Added UART5 breakout pins
    [UPD-board.kicad_pcb, UPD-board.kicad_sch, power_switching.kicad_sch]
2022-09-08 Added BOMs
    [UPD-board-digikey-x1.xlsx, UPD-board-digikey.xlsx, UPD-board-mouser-x1.xlsx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]
2022-09-08 Preparing to make changes for unavailable parts
    [UPD-board.kicad_pcb, UPD-board.kicad_sch, UPD-board.ods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]
2022-09-19 Fixed silkscreen and switched components
    [UPD-board.kicad_pcb, UPD-board.kicad_sch, power_switching.kicad_sch]
2022-09-19 UPD board is ready for production I think
    [UPD-board.kicad_pcb, UPD-board.kicad_sch, power_switching.kicad_sch]
2022-09-23 Fixed small board error
    [UPD-board.kicad_pcb]
2022-09-23 Cleaned up the repo
    [UPD-board-digikey-x1.xlsx, UPD-board-digikey.xlsx, UPD-board-mouser-x1.xlsx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]
2023-01-13 Fixed UPD board, ready for review and ordering
    [UPD-board.kicad_pcb, UPD-board.kicad_sch, power_switching.kicad_sch]
2023-01-15 Fixed pin 1 of expanders being pulldown only
    [UPD-board.kicad_pcb, UPD-board.kicad_sch, power_switching.kicad_sch]
2023-01-15 rev2.1 should be done
    [UPD-board.kicad_pcb, UPD-board.kicad_sch, power_switching.kicad_sch]
2023-01-22 Moved vias out from under test
    [UPD-board.kicad_pcb]
2023-07-31 modified schematic diagram for clarity
    [uniclogs-latching-relay-driver.kicad_sch]
2023-08-17 updated board changes for bom
    [UPD-board.kicad_sch, power_switching.kicad_sch]
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

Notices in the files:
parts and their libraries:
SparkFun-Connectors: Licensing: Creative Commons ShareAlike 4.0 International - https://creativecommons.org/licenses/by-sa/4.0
